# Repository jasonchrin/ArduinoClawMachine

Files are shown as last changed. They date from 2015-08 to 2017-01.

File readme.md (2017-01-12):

Arduino Claw Machine

The goal of this project is to build a claw machine and be able to control it via a joystick and eventually over the web.

The machine frame is based around an Ultimaker Plus 3d printer.  

I'm anticipating having the machine being driven by an Arudino MEGA and have a Raspberry Pi3 in place once I add video streaming and webcontrol.

I want to build something fun and learn something along the way.  

Checkout http://chrin.com/category/clawmachine/ for a build log

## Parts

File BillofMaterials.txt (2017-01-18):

Frame
Batlic Birch Plywood 6mm 24x30		131401	qty:3	10.50		31.50
Finnish Birch Plywood 4mm 24x30		124879	qty:1	24.99		24.99
Shipping								9.99
Tax									3.65

https://www.amazon.com/gp/product/B01FNT093A/ref=oh_aui_detailpage_o02_s00?ie=UTF8&psc=1
200mm gt2 belt					qty:1	12.88

https://www.amazon.com/gp/product/B00F2IQNX8/ref=oh_aui_detailpage_o02_s01?ie=UTF8&psc=1
5m gt2mm belt					qty:1	10.32

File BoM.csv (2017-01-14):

 | Part | UM BOM Part | sku | Qty | cost | total |  | vendor | link
Frame | Batlic Birch Plywood 6mm 24x30 | All plywood parts | 131401 | 3 | 10.5 | 31.5 |  | Woodcraft | https://www.woodcraft.com/products/baltic-birch-plywood-6mm-1-4-x-24-x-30
Frame | Finnish Birch Plywood 4mm 24x30 | All plywood parts | 124879 | 1 | 24.99 | 24.99 |  | Woodcraft | https://www.woodcraft.com/products/finnish-birch-plywood-5-32-x-24-x-30
Frame | screws, nuts, washers |  |  |  |  |  |  | ebay
Frame | Plexiglass
 |  |  |  |  |  |  | 56.49
gantry | 5PCS Aluminum GT2 Timing Belt Pulley 5mm | 1084 |  | 1 | 10.99 | 10.99 |  | Amazon | https://www.amazon.com/gp/product/B019GI5DVC/ref=oh_aui_detailpage_o06_s00?ie=UTF8&psc=1
gantry | 5PCS Aluminum GT2 Timing Belt Pulley 8mm | 1088 (x10) |  | 2 | 10.99 | 21.98 |  | Amazon | https://www.amazon.com/gp/product/B019GI5DVC/ref=oh_aui_detailpage_o06_s00?ie=UTF8&psc=1
gantry | 2Pcs LM6LUU 6mm | 1065 |  | 1 | 9.27 | 9.27 |  | Amazon | https://www.amazon.com/gp/product/B019GIJ296/ref=oh_aui_detailpage_o06_s01?ie=UTF8&psc=1
gantry | 8x11x30 bushing | 1056 |  | 2 | 4.72 | 9.44 |  | Amazon | https://www.amazon.com/uxcell-Self-lubricating-Copper-Bushing-Bearing/dp/B01FEXL6KU
gantry | Linear Motion Rod 6mm x 300mm shaft | 1046 |  | 2 | 4.96 | 9.92 |  | Amazon | https://www.amazon.com/gp/product/B01CG7C1TM/ref=oh_aui_detailpage_o08_s00?ie=UTF8&psc=1
gantry | 2-Pack - Linear Motion Rod 8 mm x 406mm Shaft | 1011 |  | 1 | 18.5 | 18.5 |  | Amazon | https://www.amazon.com/gp/product/B01I49ESN8/ref=oh_aui_detailpage_o09_s00?ie=UTF8&psc=1
gantry | 2-Pack - Linear Motion Rod 8 mm x 342 mm Shaft | 1012 |  | 1 | 16.95 | 16.95 |  | Amazon | https://www.amazon.com/gp/product/B01M34ZJKF/ref=oh_aui_detailpage_o00_s00?ie=UTF8&psc=1
gantry | 688-2RS Bearings (10pk) | 1021 |  | 1 | 10.49 | 10.49 |  | Amazon | https://www.amazon.com/8x16x5mm-Precision-Bearings-Rubber-688-2RS-BU/dp/B00ZVF8EMU
gantry | 200mm GT2 Belt loops (10pk) | 1086 (x4) |  | 1 | 12.88 | 12.88 |  | Amazon | https://www.amazon.com/gp/product/B01FNT093A/ref=oh_aui_detailpage_o02_s00?ie=UTF8&psc=1
gantry | 5M GT2 Belt | 1085 (x2) |  | 1 | 10.32 | 10.32 |  | Amazon | https://www.amazon.com/gp/product/B00F2IQNX8/ref=oh_aui_detailpage_o02_s01?ie=UTF8&psc=1
 |  |  |  |  |  |  | 130.74
electronics | Limit Switch | 1082 |  | 1 | 2.2 | 2.2 |  | Amazon | https://www.amazon.com/uxcell-Micro-Switch-Roller-Action/dp/B00E0JOTV8
electronics | Nema 17 Stepper | 1023 |  | 2 | 12.99 | 25.98 |  | Amazon | https://www.amazon.com/Stepper-Motor-Bipolar-64oz-Printer/dp/B00PNEQI7W
electronics | 10 Pin 2Bit 7 Segment LED 25x19 |  |  | 1 | 2.83 | 2.83 |  | Amazon | https://www.amazon.com/gp/product/B00HR7E30M/ref=oh_aui_detailpage_o02_s00?ie=UTF8&psc=1
electronics | Big red button |  |  | 1 | 6.55 | 6.55 |  | Amazon | https://www.amazon.com/gp/product/B008MU3UM0/ref=oh_aui_detailpage_o00_s00?ie=UTF8&psc=1
electronics | Joystick |  |  | 1 | 25.95 | 25.95 |  | Amazon | https://www.amazon.com/gp/product/B00BFL2SSA/ref=oh_aui_detailpage_o00_s01?ie=UTF8&psc=1
electronics | Green Lamp 24mm Dia Push Button |  |  | 1 | 4.95 | 4.95 |  | Amazon | https://www.amazon.com/gp/product/B008MU3Q9W/ref=od_aui_detailpages00?ie=UTF8&psc=1
electronics | 120v 10A DC power supply |  |  | 1 | 12.99 | 12.99 |  | Amazon | https://www.amazon.com/gp/product/B008MU0CHG/ref=oh_aui_detailpage_o08_s00?ie=UTF8&psc=1
electronics | 74HC595 8bit Shft Register |  |  | 1 | 5.95 | 5.95 |  | Amazon | https://www.amazon.com/gp/product/B00HPPOXM4/ref=oh_aui_detailpage_o07_s00?ie=UTF8&psc=1
electronics | 30pc 2.54 DIP IC socket |  |  | 1 | 10.42 | 10.42 |  | Amazon | https://www.amazon.com/gp/product/B0079SM1LW/ref=oh_aui_detailpage_o05_s00?ie=UTF8&psc=1
electronics | Arduino Mega |  |  | 1 | 27.22 | 27.22 |  | Amazon | https://www.amazon.com/ARDUINO-A000067-ATMEGA2560-2560-R3/dp/B0046AMGW0?s=pc
electronics | EasyDriver |  |  | 2 | 8 | 16 |  | Amazon | https://www.amazon.com/gp/product/B004G4XR60/ref=oh_aui_detailpage_o00_s00?ie=UTF8&psc=1
electronics | raspberry pi
electronics | drop motor
electronics | wiring
 |  |  |  |  |  |  | 141.04
 |  |  |  |  |  |  | 328.27

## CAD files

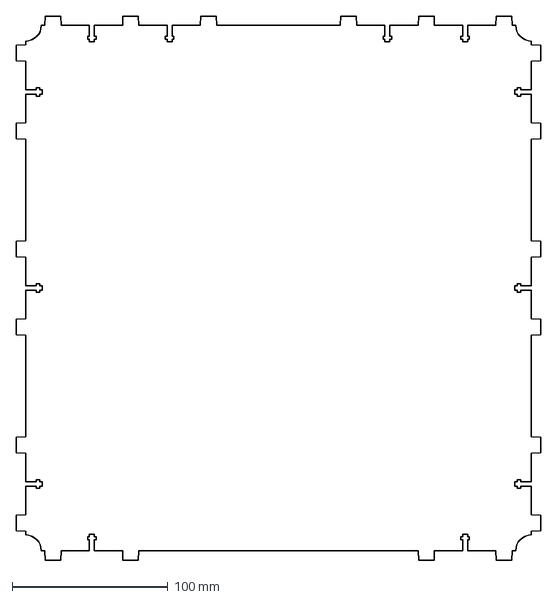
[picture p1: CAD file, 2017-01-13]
Drawings/dwg/frame1-36.dxf
337.2 x 349.7 mm

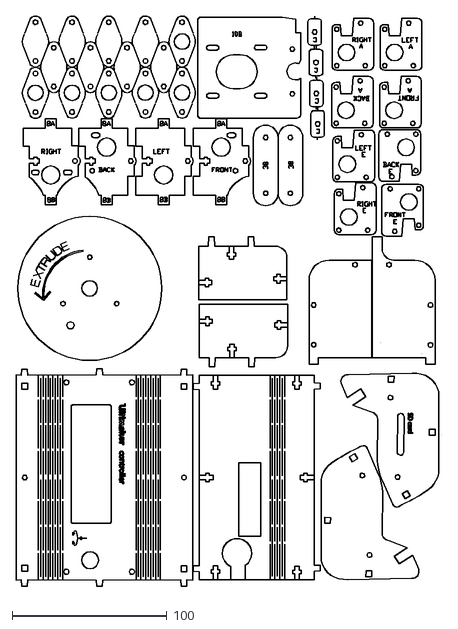
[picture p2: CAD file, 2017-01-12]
Drawings/dxf/laser files Ultimaker Original +/14Ulti-Kelpi-4mm.dxf
274.6 x 370.1

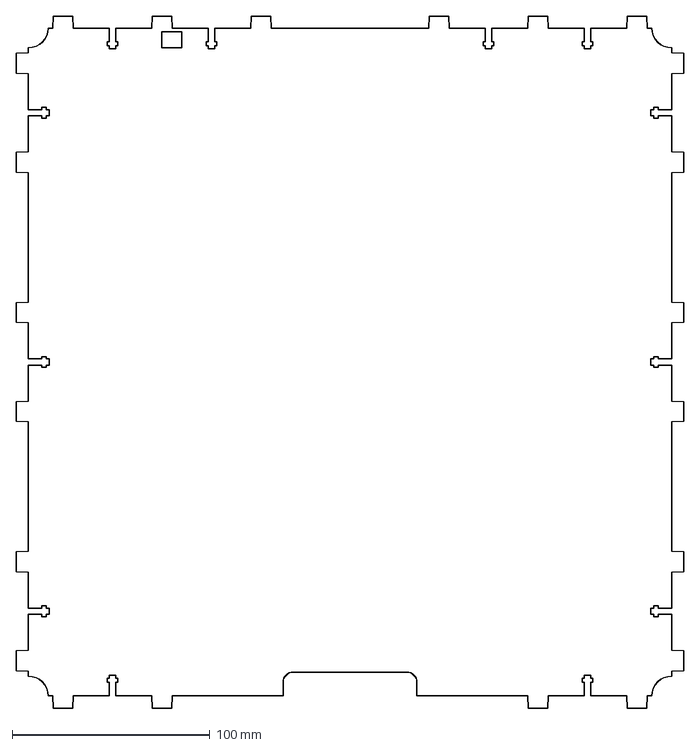
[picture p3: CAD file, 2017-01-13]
Drawings/dwg/frame1.dxf
337.2 x 349.7 mm

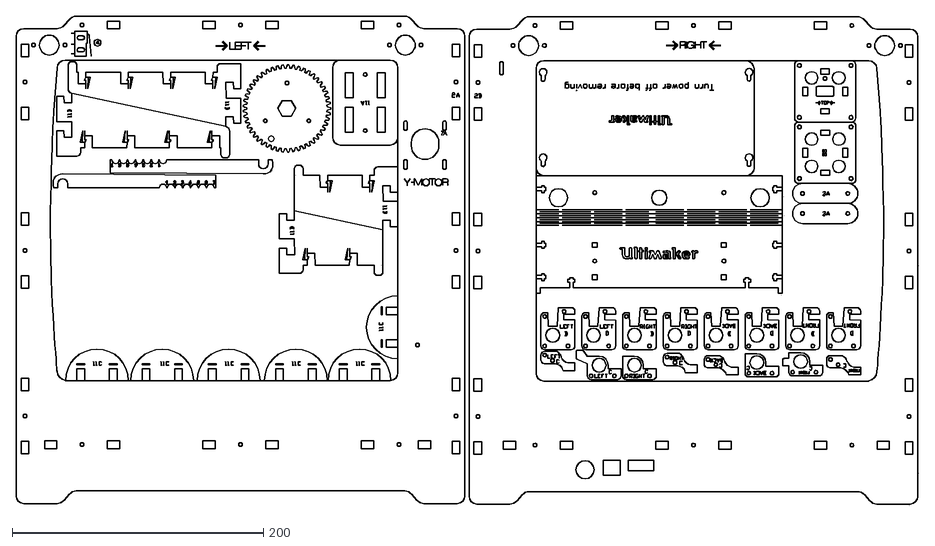
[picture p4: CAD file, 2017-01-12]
Drawings/dxf/laser files Ultimaker Original +/14Ulti-Kelpi-LeftRight.dxf
718.6 x 389.8

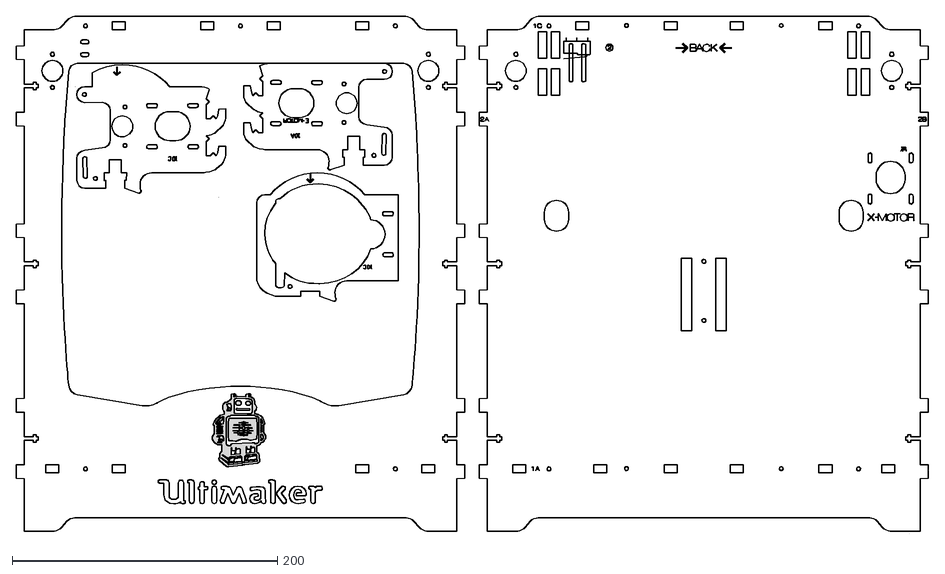
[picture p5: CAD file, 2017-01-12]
Drawings/dxf/laser files Ultimaker Original +/14Ulti-Kelpi-Front Back .dxf
688.5 x 390.0

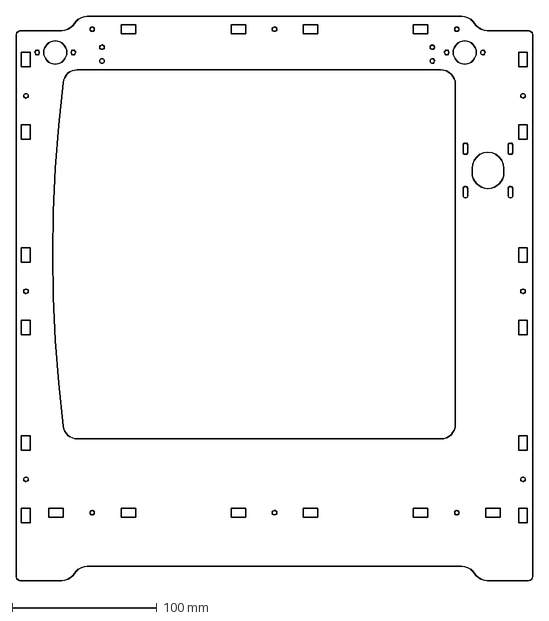
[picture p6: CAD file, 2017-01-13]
Drawings/dwg/frame4.dxf
357.0 x 390.0 mm

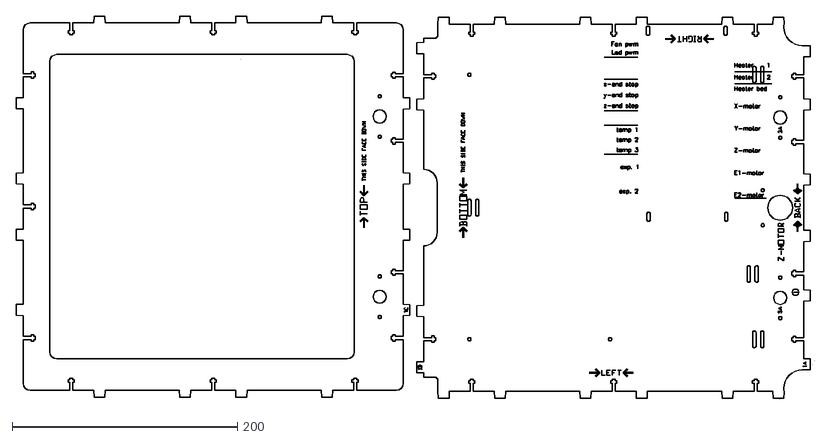
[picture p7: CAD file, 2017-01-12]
Drawings/dxf/laser files Ultimaker Original +/14Ulti-Kelpi-TopBottom.dxf
709.2 x 341.0

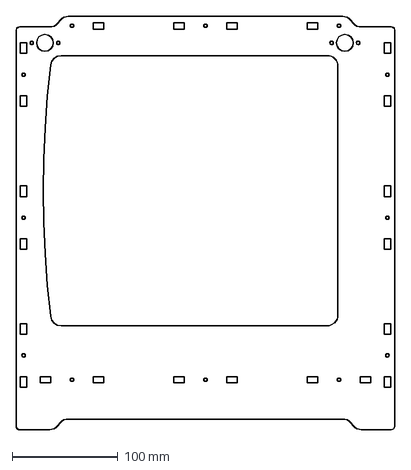
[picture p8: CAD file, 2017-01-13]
Drawings/dwg/frame5.dxf
357.0 x 390.0 mm

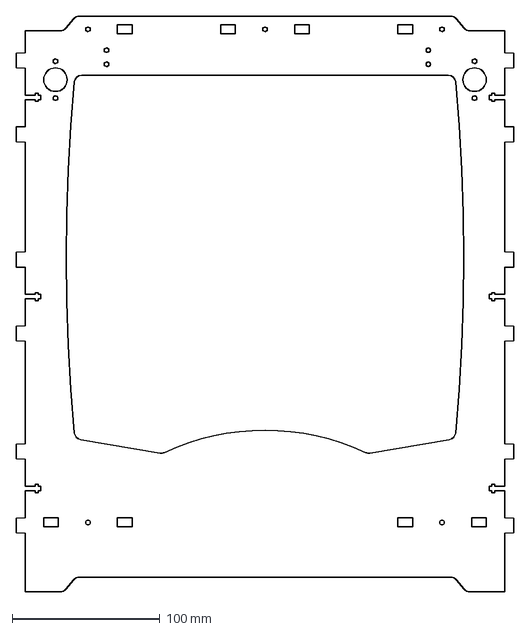
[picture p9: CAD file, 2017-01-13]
Drawings/dwg/frame2.dxf
337.2 x 390.0 mm

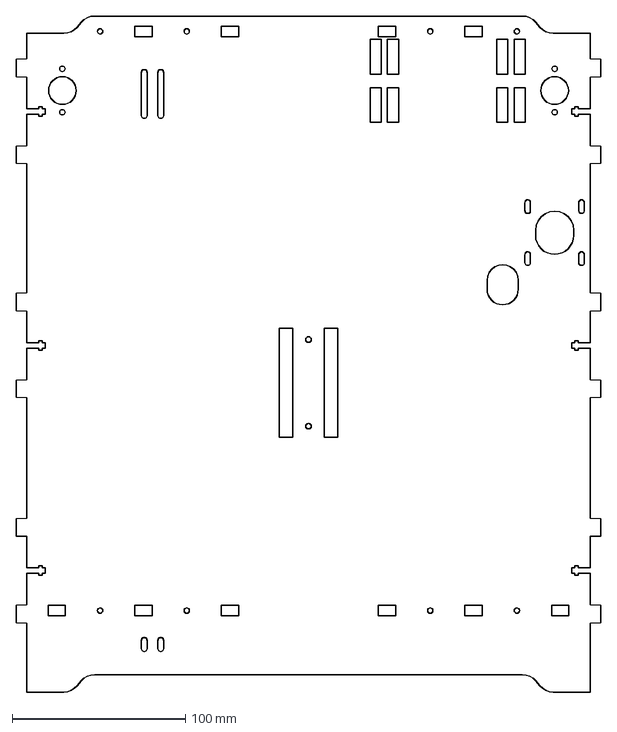
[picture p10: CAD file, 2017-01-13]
Drawings/dwg/frame3.dxf
337.2 x 390.0 mm

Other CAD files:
Drawings/dwg/frame5-36.dwg
Drawings/dwg/frame4-36.dwg
Drawings/dwg/frame2-36.dwg
Drawings/dwg/frame1-36.dwg
Drawings/dwg/frame2-.dwg

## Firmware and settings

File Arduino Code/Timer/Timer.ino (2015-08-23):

#define ledDigitsData 2
#define ledDigitsLatch 3
#define ledDigitsClock 4
#define clawButton 6
#define ledDigitsOne 8
#define ledDigitsTwo 9
#define startButtonLed 10
#define startButton 11
#define clawButtonLed 12
#define baseClockTime 45

int startingTime; 
int DisplayDigits[] = {192, 249, 164, 176, 153, 146, 130, 248, 128, 152};

void setup() {
  startingTime = 0;

  pinMode(ledDigitsLatch, OUTPUT);
  pinMode(ledDigitsClock, OUTPUT);
  pinMode(ledDigitsData, OUTPUT);
  pinMode(ledDigitsOne, OUTPUT);
  pinMode(ledDigitsTwo, OUTPUT);
  pinMode(startButtonLed, OUTPUT);
  pinMode(clawButtonLed, OUTPUT);
  pinMode(startButton, INPUT);
  pinMode(clawButton, INPUT);
  TIMSK1=0x01; // enabled global and timer overflow interrupt;
  TCCR1A = 0x00; // normal operation page 148 (mode0);
  TCNT1=0x0BDC; // set initial value to remove time error (16bit counter register)
  TCCR1B = 0x00; // start timer/ set clock
  Serial.begin(9600); //Open Serial connection for debugging
  digitalWrite(startButtonLed, HIGH);
  digitalWrite(clawButtonLed, LOW);
  digitalWrite(ledDigitsOne, LOW);
  digitalWrite(ledDigitsTwo, LOW);
}

void loop() {
  if(startingTime > 0){
    IsClawButtonPressed();
    DisplayTimer(startingTime);
  }else{
    StopTimerDisplay();
    IsStartButtonPressed();
  }
}

void IsStartButtonPressed(){
  int buttonState = digitalRead(startButton);
  if(buttonState == HIGH){
   StartButtonPress();
  }
}

void StartButtonPress(){
  Serial.println("START PRESS");
  TCCR1B = 0x04; 
  startingTime = baseClockTime;
  digitalWrite(startButtonLed, LOW);
  digitalWrite(clawButtonLed, HIGH);
}

void IsClawButtonPressed(){
  int pressState = digitalRead(clawButton);
  if(pressState == HIGH){
    ClawButtonPress();
  }
}
void ClawButtonPress(){
  Serial.println("CLAW PRESS");
  startingTime = 0;
  StopTimerDisplay();
}

void StopTimerDisplay(){
  TCCR1B = 0x00; // start timer/ set clock
  digitalWrite(ledDigitsOne, LOW);
  digitalWrite(ledDigitsTwo, LOW);
  digitalWrite(startButtonLed, HIGH);
  digitalWrite(clawButtonLed, LOW);
}

ISR(TIMER1_OVF_vect) {
  TCNT1=0x0BDC; // set initial value to remove time error (16bit counter register)
  startingTime = startingTime - 1;
}

void DisplayTimer(int displayTime){
  int firstDigit = 0;
  if(displayTime > 9){
    firstDigit = displayTime/10;
  }
  int secondDigit = displayTime - firstDigit*10;

  DisplayDigit(ledDigitsOne, DisplayDigits[firstDigit]);
  DisplayDigit(ledDigitsTwo, DisplayDigits[secondDigit]);  
}

void DisplayDigit(int pinNo, int number){
  digitalWrite(ledDigitsOne, LOW);
  digitalWrite(ledDigitsTwo, LOW);
  digitalWrite(ledDigitsLatch, LOW);
  shiftOut(ledDigitsData, ledDigitsClock, MSBFIRST, number);  
  digitalWrite(ledDigitsLatch, HIGH);
  digitalWrite(pinNo, HIGH);
  digitalWrite(ledDigitsLatch, LOW);
  delay(10);
}

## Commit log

2015-08-18 Add initial sketch-up drawing of parts that will be laser cut
2015-08-23 Arduino simple countdown working with start/stop buttons
2017-01-12 Add resources
    forks from ultimaker and laser exports
    [14Ulti-Kelpi-4mm.dxf, 14Ulti-Kelpi-Front Back .dxf, 14Ulti-Kelpi-LeftRight.dxf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]
2017-01-13 Add dwg
    Did some work in Draftsight to remove a few cutouts that aren't
    necessary, move the bottom up 36mm, and start work on the chute
    [frame1-36.dwg, frame1-36.dxf, frame1.dxf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]
2017-01-14 start of Bill of Materials
    [BoM.csv]
2017-01-14 Bom Update
    [BoM.csv]
2017-01-18 update bom, drawing update
